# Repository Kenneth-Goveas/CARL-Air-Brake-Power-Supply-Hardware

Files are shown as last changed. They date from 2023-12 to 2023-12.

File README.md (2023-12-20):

# CARL Air Brake Power Supply Hardware

This repository contains the electronic hardware design for the power supply
module of the [CARL Air Brake][cab-repo] computer. The CARL Air Brake computer
automatically controls a rocket air brake in flight, so that the vehicle attains
an apogee at the desired altitude. The power supply module distributes
electrical power to all systems in the computer.

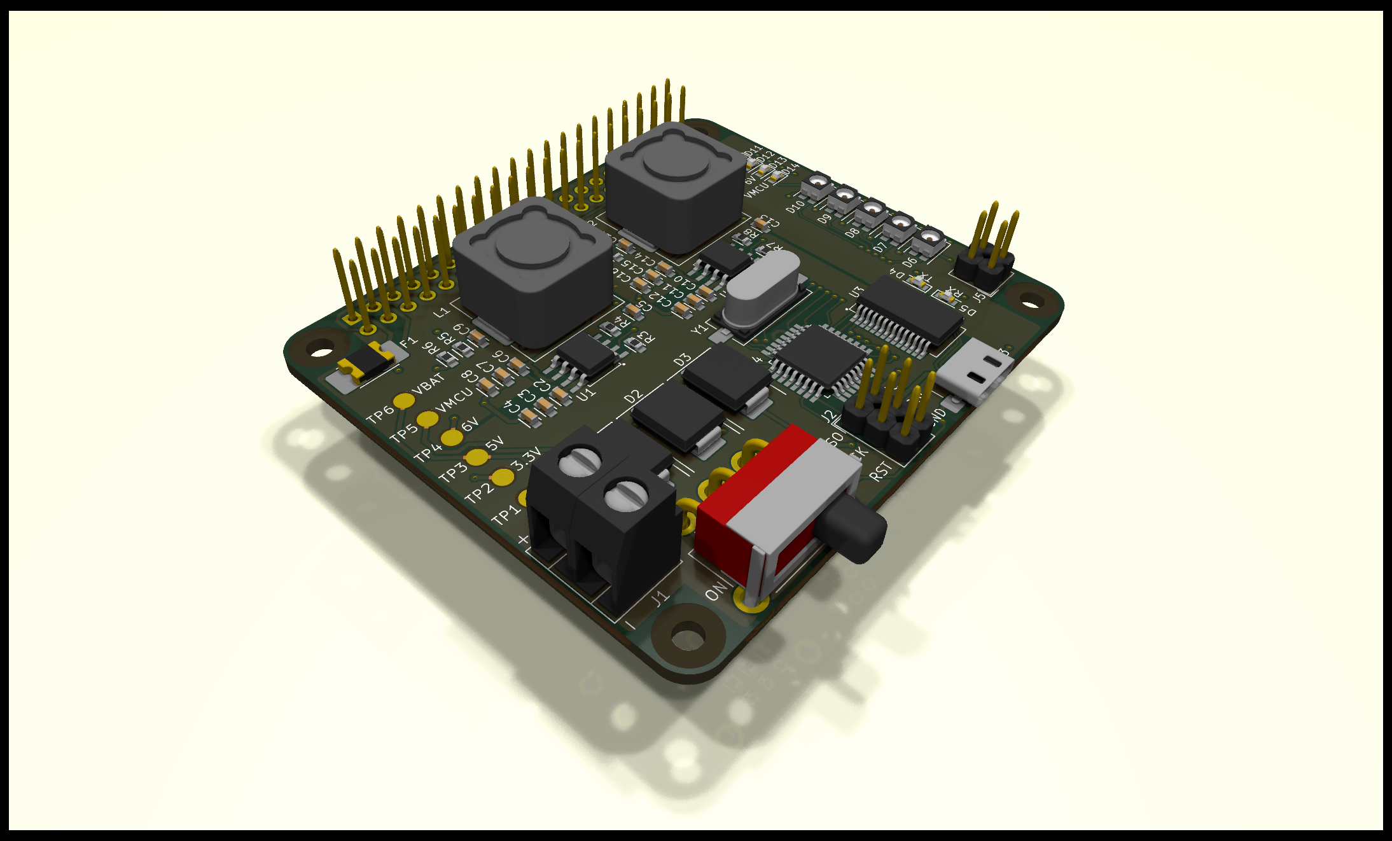
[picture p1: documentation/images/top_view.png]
Top view of the power supply module


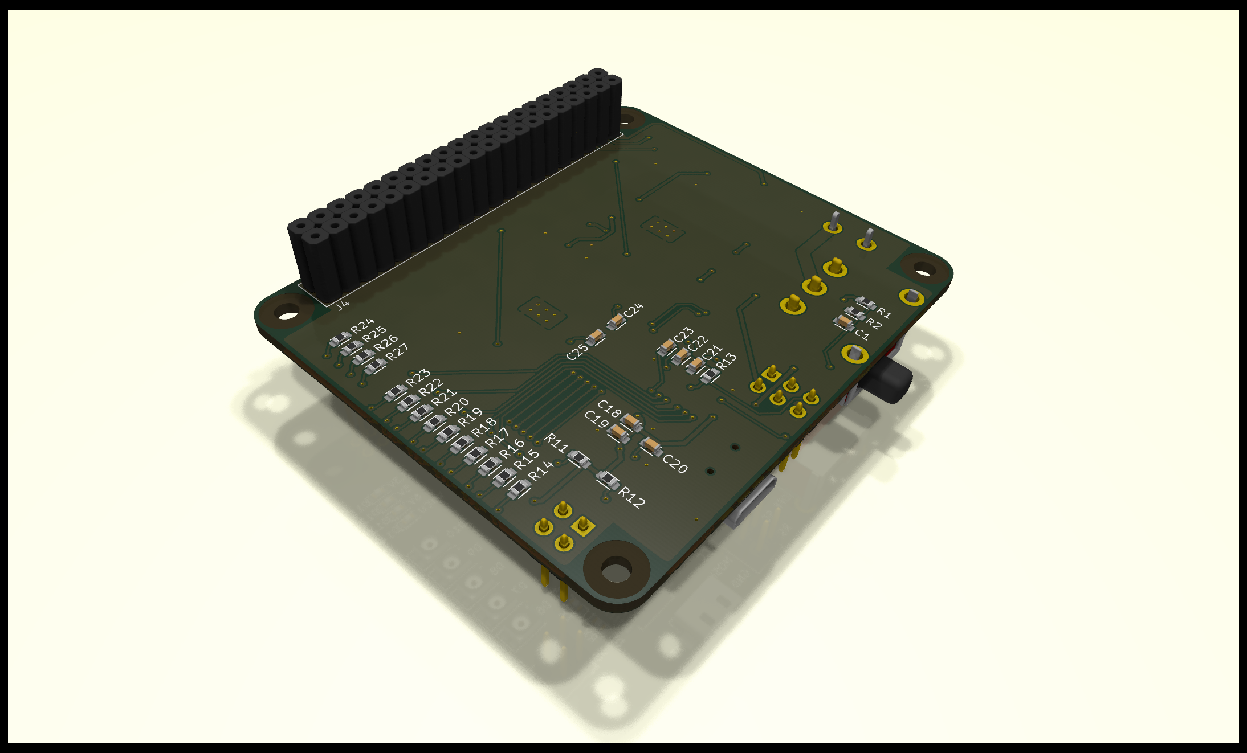
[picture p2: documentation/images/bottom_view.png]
Bottom view of the power supply module


Detailed documentation for this repository can be found in the following files.

- [description.md][des]:
  Detailed description of the power supply module.
- [cloning.md][cln]:
  Properly cloning this repository along with all its submodules.
- [prerequisites.md][req]:
  Necessary software for viewing and editing the electronic design.
- [organization.md][org]:
  Directory structure and organization of files in this repository.
- [flashing.md][fsh]:
  Flashing software onto the power supply module.

[des]:      ./documentation/description.md
[cln]:      ./documentation/cloning.md
[req]:      ./documentation/prerequisites.md
[org]:      ./documentation/organization.md
[fsh]:      ./documentation/flashing.md

[cab-repo]: https://github.com/Kenneth-Goveas/CARL-Air-Brake

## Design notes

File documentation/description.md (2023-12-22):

# Description

The CARL Air Brake computer is comprised of the following three circuit boards.
These boards are loaded with their respective software and connected by stacking
on top of each other, to make up the computer.

- Peripheral devices module.
- Power supply module.
- Raspberry Pi 3 model A+.

This repository contains the electronic design for the second of the above three
boards. Other electronic designs and software are contained in different
repositories (for more details, see [CARL Air Brake][cab-repo]).

## Overview

The power supply module supplies regulated power to all systems in the CARL Air
Brake computer. It also has status LEDs to indicate which of the onboard power
lines are live. After being flashed with its associated software, it also
monitors the battery voltage and indicates the same on another LED array. When
the battery is fully charged, all these LEDs light up in green. As the voltage
drops, they turn red one by one. When all these LEDs turn red, they also start
flashing to indicate to the user that the battery needs charging.

## Battery

The power supply module is intended for use with a lithium polymer battery with
the following specifications.

| **Specification** | **Value** |
| --- | --- |
| Cells in series | 3 |
| Nominal voltage | 11.1V |
| Fully charged voltage | 12.6V |
| Continuous discharge current  | >1.5A |

## Components

The relevant circuit components on the board are marked on the following diagram
and described below.

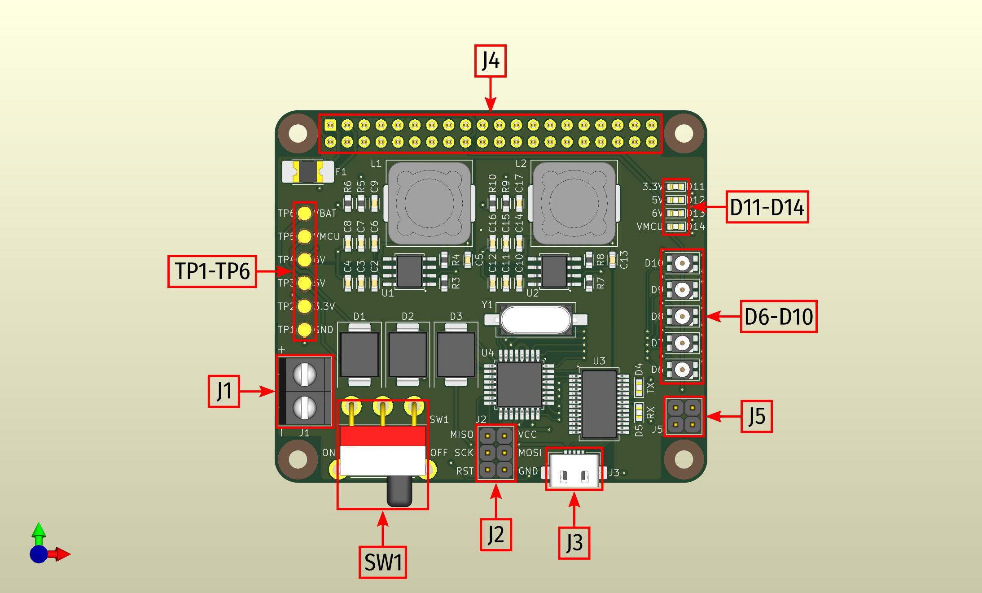
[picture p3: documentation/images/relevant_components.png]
Relevant components of the power supply module


| **Designation** | **Description** |
| --- | --- |
| J1 | Screw terminal for battery connection. |
| J2 | Port for ICSP cable for programming. |
| J3 | Port for USB cable for programming. |
| J4 | Stacking header for connecting other boards. |
| J5 | Header for supplying 6V to peripheral devices module. |
| SW1 | Switch for making/breaking battery connection. |
| D6-D10 | Battery voltage indication LEDs. |
| D11-D14 | Power line status LEDs. |
| TP1-TP6 | Test points for measuring power line voltages. |

## Working

The following is a simple block diagram of the power supply module.

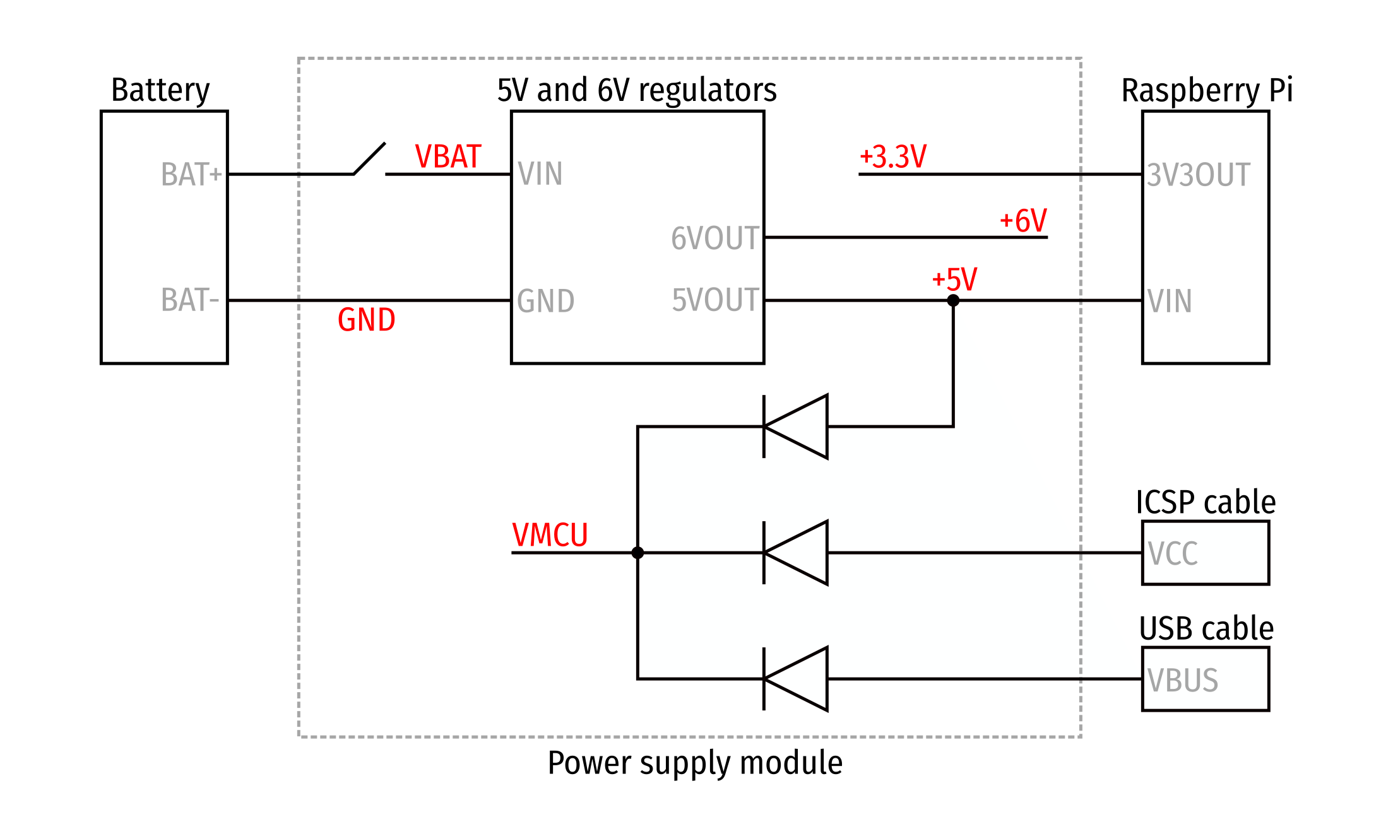
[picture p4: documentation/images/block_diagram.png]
Block diagram of the power supply module


As seen in the above diagram, the board contains the following five power lines.
Note that the line voltages listed below are nominal values. It is normal for
the actual voltages to deviate slightly.

| **Name**  | **Description** | **Voltage** |
| --- | --- | --- |
| VBAT | Positive terminal of battery. | Battery voltage |
| +3.3V | Output of 3.3V regulator on Raspberry Pi. | 3.3V |
| +5V | Output of onboard 5V regulator. | 5V |
| +6V | Output of onboard 6V regulator. | 6V |
| VMCU | Power line for onboard microcontroller. | 5V |

When the battery is connected and the switch turned on, the VBAT, VMCU, +5V, and
+6V lines become live. If, in addition to the battery, the Raspberry Pi is also
connected, then the +3.3V line also becomes live. If any or both of the two
programming cables are connected, the VMCU line becomes live regardless of
whether or not the battery is connected. Thus, the VMCU line has three power
sources - the battery, and two programming cables. It is safe to simultaneously
connect more than one of these power sources as the board has protection diodes
that will prevent any short circuit.

The Raspberry Pi draws power from the +5V line. The Raspberry Pi has an onboard
3.3V regulator which supplies power to the +3.3V line. The peripheral devices
module draws power from the +3.3V, +5V, and +6V lines. The VMCU line supplies
power to the onboard microcontroller of the power supply module, and its
associated circuitry. Each regulated power line is also connected to a separate
status LED (D11-D14) to visually indicate which lines are live. Additionally,
all power and GND lines are connected to separate test points (TP1-TP6) for
measuring their voltages with a multimeter.

The onboard microcontroller is programmable from the two ports J2 and J3. When
flashed with the appropriate software (see [flashing.md][fsh]), it measures the
battery voltage and accordingly drives the indication LEDs (D6-D10), resulting
in the behavior described in [Overview](#overview).

[fsh]:      ./flashing.md

[cab-repo]: https://github.com/Kenneth-Goveas/CARL-Air-Brake

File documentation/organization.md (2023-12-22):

# Organization

Upon properly cloning this repository according to the instructions in
[cloning.md][cln], you should end up with the following directory structure.

```
CARL-Air-Brake-Power-Supply-Hardware/
|__ CARL-Air-Brake-Power-Supply-Hardware.kicad_pro
|__ CARL-Air-Brake-Power-Supply-Hardware.kicad_sch
|__ CARL-Air-Brake-Power-Supply-Hardware.kicad_pcb
|__ production/
|   |__ CARL-Air-Brake-Power-Supply-Hardware.bom.csv
|   |__ CARL-Air-Brake-Power-Supply-Hardware.boardoutline.ger
|   |__ CARL-Air-Brake-Power-Supply-Hardware.toplayer.ger
|   |__ CARL-Air-Brake-Power-Supply-Hardware.bottomlayer.ger
|   |__ CARL-Air-Brake-Power-Supply-Hardware.topsoldermask.ger
|   |__ CARL-Air-Brake-Power-Supply-Hardware.bottomsoldermask.ger
|   |__ CARL-Air-Brake-Power-Supply-Hardware.toppaste.ger
|   |__ CARL-Air-Brake-Power-Supply-Hardware.bottompaste.ger
|   |__ CARL-Air-Brake-Power-Supply-Hardware.topsilkscreen.ger
|   |__ CARL-Air-Brake-Power-Supply-Hardware.bottomsilkscreen.ger
|   |__ CARL-Air-Brake-Power-Supply-Hardware.drills_pth.xln
|   |__ CARL-Air-Brake-Power-Supply-Hardware.holes_npth.xln
|__ fp-lib-table -> ./library/fp-lib-table
|__ sym-lib-table -> ./library/sym-lib-table
|__ library/
|   |__ symbols/
|   |__ footprints/
|   |__ models/
|   |__ fp-lib-table
|   |__ sym-lib-table
|   |__ README.md
|__ README.md
|__ documentation/
    |__ images/
    |__ description.md
    |__ cloning.md
    |__ prerequisites.md
    |__ organization.md
    |__ flashing.md
```

The KiCad project, schematic, and board files are located in the root directory.
The bill of materials file, and the gerber and drill files for production are
located in the [production][prod-dir] directory. The KiCad component library
[KiCad Libraries][lib-repo] is contained as a submodule in the
[library][lib-dir] directory. Symbolic links [fp-lib-table][fp-lnk] and
[sym-lib-table][sym-lnk] in the root directory point to the library table files
[fp-lib-table][fp-file] and [sym-lib-table][sym-file] in the [library][lib-dir]
directory. These symbolic links are required for KiCad to be able to locate the
component library.

[cln]:      ./cloning.md

[prod-dir]: ../production

[fp-lnk]:   ../fp-lib-table
[sym-lnk]:  ../sym-lib-table
[fp-file]:  ../library/fp-lib-table
[sym-file]: ../library/sym-lib-table

[lib-dir]:  ../library
[lib-repo]: https://github.com/Kenneth-Goveas/KiCad-Libraries

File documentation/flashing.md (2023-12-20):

# Flashing

The software for the power supply module can be found in the
[CARL Air Brake Power Supply Software][cab-psup-sw-repo] repository. This
repository contains two programs - a tuning program, and a main program - that
can be flashed onto the board. The tuning program is used to calibrate the
voltage thresholds at which the indication LEDs should turn red. The main
program is used to monitor the battery voltage and drive the LEDs as described
in [description.md][des]. For detailed instructions for flashing the software,
see [CARL Air Brake Power Supply Software][cab-psup-sw-repo].

[des]:              ./description.md

[cab-psup-sw-repo]: https://github.com/Kenneth-Goveas/CARL-Air-Brake-Power-Supply-Software

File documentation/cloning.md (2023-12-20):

# Cloning

This repository contains symbolic links, and also includes other repositories as
submodules. Therefore, special care needs to be taken to properly clone this
repository onto a local system. In particular, Git must be configured to
preserve symbolic links, and submodules must be cloned recursively.

## Configuring Git

The following command configures Git to preserve symbolic links. On Windows, it
may also be necessary to enable [Developer mode][win-dev-mode] to allow the
creation of symbolic links.

```
git config --global core.symlinks true
```

## Cloning recursively

Once Git is configured as above, the following command properly clones this
repository along with all its submodules. Note that the `--recurse-submodules`
option is passed to clone submodules recursively.

```
git clone --recurse-submodules \
  https://github.com/Kenneth-Goveas/CARL-Air-Brake-Power-Supply-Hardware.git
```

[win-dev-mode]: https://learn.microsoft.com/en-us/windows/apps/get-started/enable-your-device-for-development

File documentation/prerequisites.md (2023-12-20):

# Prerequisites

The electronic design in this repository was created with [KiCad 7.0][kicad],
which must be installed on your system in order to view and edit the design.
Installation instructions can be found on the [Download][kicad-dl] page.

Additionally, the [Fira Sans Condensed][fira] font was used in the KiCad
schematic and symbol editors instead of the default font. This is because the
default font occupies more space, making it difficult to fit the schematic on
the page. Once installed, this font can be selected in KiCad by clicking on
*Preferences > Preferences > Schematic Editor > Display Options* and choosing
from the *Default font* drop down menu.

[kicad]:    https://www.kicad.org
[kicad-dl]: https://www.kicad.org/download

[fira]:     https://fonts.google.com/specimen/Fira+Sans+Condensed

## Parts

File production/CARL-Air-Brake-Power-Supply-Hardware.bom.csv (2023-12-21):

Serial | Reference | Manufacturer | Part | Description | Quantity
1 | R24 | Yageo | AC0603FR-0768RL | Resistor 68Ohm 100mW 1% 0603 | 1
2 | R14 R15 R16 R17 R18 R19 R20 R21 R22 R23 R25 R27 | Yageo | RC0603FR-10150RL | Resistor 150Ohm 100mW 1% 0603 | 12
3 | R26 | Yageo | RC0603FR-07200RL | Resistor 200Ohm 100mW 1% 0603 | 1
4 | R11 R12 | Yageo | RT0603DRE07430RL | Resistor 430Ohm 100mW 0.5% 0603 | 2
5 | R2 R3 R7 R13 | Yageo | RT0603FRE1310KL | Resistor 10kOhm 100mW 1% 0603 | 4
6 | R1 | Yageo | RC0603FR-1320KL | Resistor 20kOhm 100mW 1% 0603 | 1
7 | R6 R10 | Yageo | RT0603BRD0750KL | Resistor 50kOhm 100mW 0.1% 0603 | 2
8 | R4 R8 | Yageo | RC0603FR-07100KL | Resistor 100kOhm 100mW 1% 0603 | 2
9 | R5 | Yageo | AC0603FR-07365KL | Resistor 365kOhm 100mW 1% 0603 | 1
10 | R9 | Yageo | RC0603FR-07453KL | Resistor 453kOhm 100mW 1% 0603 | 1
11 | C9 C17 | Murata | GRM1885C1H5R0WA01D | Capacitor 5pF 50V 1% 0603 | 2
12 | C24 C25 | Murata | GRM1885C1H300GA01D | Capacitor 30pF 50V 2% 0603 | 2
13 | C4 C6 C12 C14 C19 C20 C23 | Murata | GCM188R71C104JA37D | Capacitor 0.1uF 16V 5% 0603 | 7
14 | C5 C13 | Murata | GRM188R61A474JA61D | Capacitor 0.47uF 10V 5% 0603 | 2
15 | C1 C2 C3 C10 C11 C18 C21 C22 | Murata | GRT188R61C106KE13J | Capacitor 10uF 16V 10% 0603 | 8
16 | C7 C8 C15 C16 | Murata | GRM188R61A226ME15D | Capacitor 22uF 10V 20% 0603 | 4
17 | L1 L2 | Eaton | DR127-3R3-R | Inductor 3.3uH 10.5A (rms) 21.5A (sat) 20% | 2
18 | F1 | Bourns | MF-MSMF260-2 | Fuse PTC 2.6A (hold) 5.2A (trip) 6V 1812 | 1
19 | D1 D2 D3 | Diotec | SK84-AQ | Diode Schottky 0.55V @ 8A DO-214AB/SMC | 3
20 | D4 D5 | Ams Osram | LW Q38G-Q1OO-3K6L-1 | LED White 2.85V @ 5mA 0603 | 2
21 | D11 D12 D13 D14 | Wuerth | 150060AS75000 | LED Amber 2V @ 20mA 0603 | 4
22 | D6 D7 D8 D9 D10 | Wuerth | 150141RV73100 | LED Red Green 2V @ 20mA | 5
23 | Y1 | ECS | ECS-160-20-5PX-TR | Crystal 16Mhz 20pF HC49-US | 1
24 | J2 | Adam Tech | PH2-06-UA | Pin Header 2x3 | 1
25 | J1 | CUI | TB003-500-P02BE | Screw Terminal 2-Pin | 1
26 | J3 | Wuerth | 629105136821 | Micro USB Receptacle | 1
27 | J4 | Adafruit | 2223 | Stacking Header 2x20 | 1
28 | J5 | Wuerth | 61300421121 | Pin Header 2x2 | 1
29 | SW1 | Salecom | T80-S-TS-13P-A1-2-R-E-H | Switch SPDT | 1
30 | U1 U2 | TI | TPS56528DDAR | Buck converter | 2
31 | U3 | FTDI | FT232RNL-REEL | USB-UART Bridge | 1
32 | U4 | Microchip | ATmega328P-AU | 8-Bit AVR Microcontroller | 1

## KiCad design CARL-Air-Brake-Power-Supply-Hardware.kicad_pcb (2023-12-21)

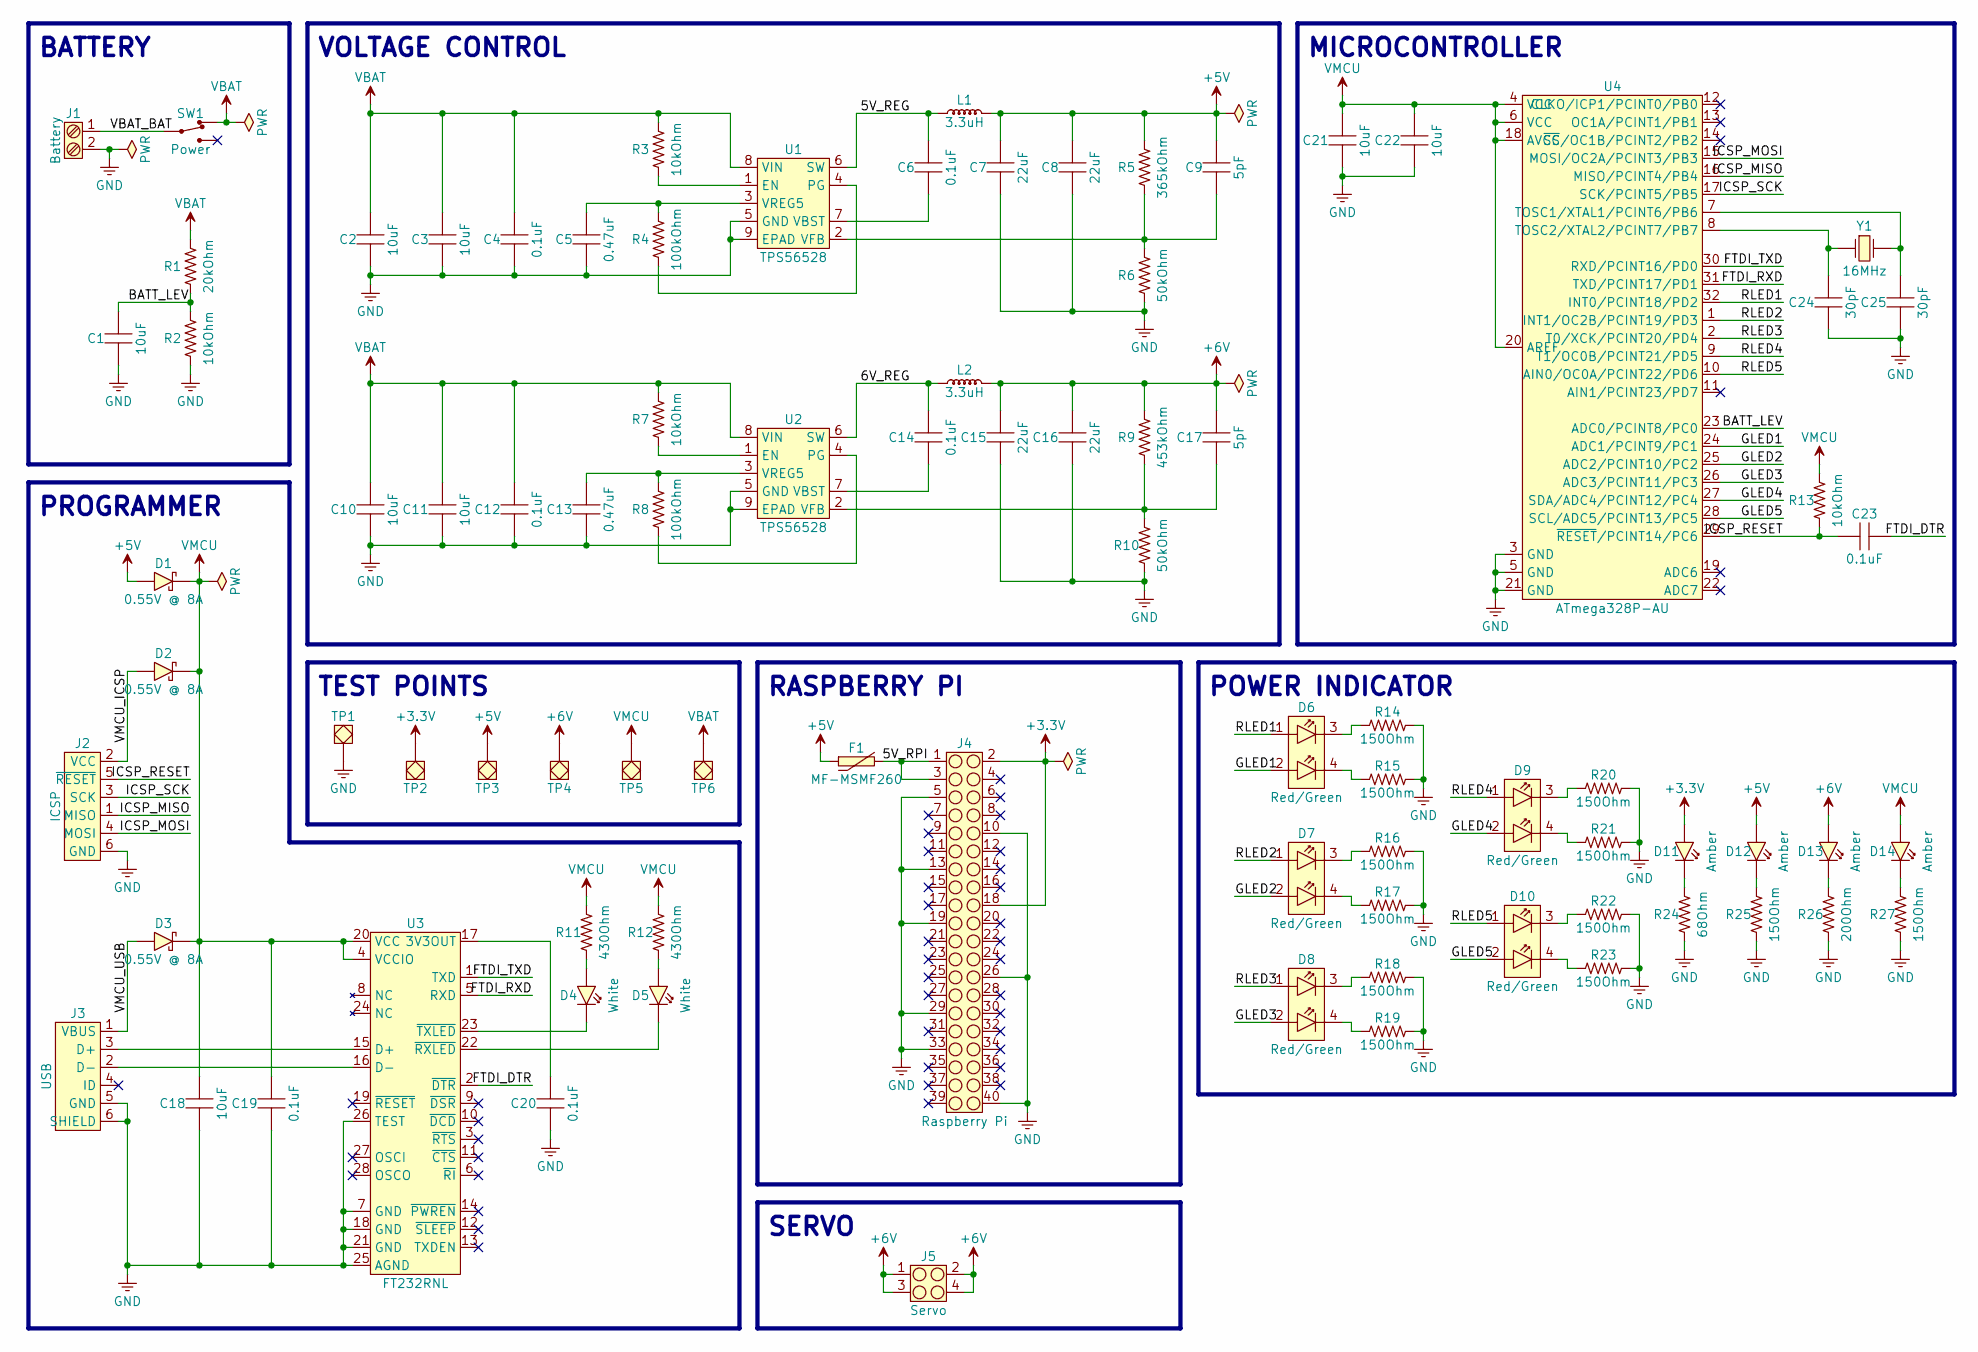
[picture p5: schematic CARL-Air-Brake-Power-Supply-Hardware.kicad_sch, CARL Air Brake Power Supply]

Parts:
C1, C2, C3, C10, C11, C18, C21, C22: 10uF; Cap_Ceramic_0603
C4, C6, C12, C14, C19, C20, C23: 0.1uF; Cap_Ceramic_0603
C5, C13: 0.47uF; Cap_Ceramic_0603
C7, C8, C15, C16: 22uF; Cap_Ceramic_0603
C9, C17: 5pF; Cap_Ceramic_0603
C24, C25: 30pF; Cap_Ceramic_0603
D1, D2, D3: 0.55V @ 8A; Diode_DO-214AB_SMC
D4, D5: White; LED_0603
D6, D7, D8, D9, D10: Red/Green; LED_Dual_Wuerth_WL-SBTW
D11, D12, D13, D14: Amber; LED_0603
F1: MF-MSMF260; Fuse_PTC_1812
J1: Battery; ScrewTerm_02_CUI_TB003-500-02BK
J2: ICSP; PinHead_02x03_Pitch2.54mm_Bot3.00mm_Top6.00mm_Shroud2.50mm
J3: USB; USB_Micro_B_Recp_Wuerth_629105136821
J4: Raspberry Pi; StackHead_02x20_Pitch2.54mm_Bot10.50mm_Top8.50mm
J5: Servo; PinHead_02x02_Pitch2.54mm_Bot3.00mm_Top6.00mm_Shroud2.50mm
L1, L2: 3.3uH; Ind_Eaton_DR127
R1: 20kOhm; Res_Film_0603
R2, R3, R7, R13: 10kOhm; Res_Film_0603
R4, R8: 100kOhm; Res_Film_0603
R5: 365kOhm; Res_Film_0603
R6, R10: 50kOhm; Res_Film_0603
R9: 453kOhm; Res_Film_0603
R11, R12: 430Ohm; Res_Film_0603
R14, R15, R16, R17, R18, R19, R20, R21, R22, R23, R25, R27: 150Ohm; Res_Film_0603
R24: 68Ohm; Res_Film_0603
R26: 200Ohm; Res_Film_0603
SW1: Power; Switch_SPDT_Salecom_T80-S-TS-13P-A1-2-R
TP1, TP2, TP3, TP4, TP5, TP6: TestPoint_CircPad2.00mm_CircMsk2.50mm
U1, U2: TPS56528; SOIC_08_Dim4.00x5.00x1.70mm_Pitch1.27mm_RectThPad2.95x4.90m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
U3: FT232RNL; SOIC_28_Dim5.50x10.50x2.00mm_Pitch0.65mm
U4: ATmega328P-AU; TQFP_08x08_Dim7.00x7.00x1.20mm_Pitch0.80mm
Y1: 16MHz; Crystal_HC49-US

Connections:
/5V_REG: C6.2, L1.1, U1.6 (SW)
/5V_RPI: F1.2, J4.1, J4.3
/6V_REG: C14.2, L2.1, U2.6 (SW)
/BATT_LEV: C1.2, R1.1, R2.2, U4.23 (ADC0/PCINT8/PC0)
/FTDI_DTR: C23.2, U3.2 (~DTR)
/FTDI_RXD: U3.5 (RXD), U4.31 (TXD/PCINT17/PD1)
/FTDI_TXD: U3.1 (TXD), U4.30 (RXD/PCINT16/PD0)
/GLED1: D6.2 (A), U4.24 (ADC1/PCINT9/PC1)
/GLED2: D7.2 (A), U4.25 (ADC2/PCINT10/PC2)
/GLED3: D8.2 (A), U4.26 (ADC3/PCINT11/PC3)
/GLED4: D9.2 (A), U4.27 (SDA/ADC4/PCINT12/PC4)
/GLED5: D10.2 (A), U4.28 (SCL/ADC5/PCINT13/PC5)
/ICSP_MISO: J2.1 (MISO), U4.16 (MISO/PCINT4/PB4)
/ICSP_MOSI: J2.4 (MOSI), U4.15 (MOSI/OC2A/PCINT3/PB3)
/ICSP_RESET: C23.1, J2.5 (~RESET), R13.1, U4.29 (~RESET/PCINT14/PC6)
/ICSP_SCK: J2.3 (SCK), U4.17 (SCK/PCINT5/PB5)
/RLED1: D6.1 (A), U4.32 (INT0/PCINT18/PD2)
/RLED2: D7.1 (A), U4.1 (INT1/OC2B/PCINT19/PD3)
/RLED3: D8.1 (A), U4.2 (T0/XCK/PCINT20/PD4)
/RLED4: D9.1 (A), U4.9 (T1/OC0B/PCINT21/PD5)
/RLED5: D10.1 (A), U4.10 (AIN0/OC0A/PCINT22/PD6)
/VBAT_BAT: J1.1, SW1.2
/VMCU_ICSP: D2.1 (A), J2.2 (VCC)
/VMCU_USB: D3.1 (A), J3.1 (VBUS)
unnamed: D4.1 (A), R11.1
unnamed: D4.2 (K), U3.23 (~TXLED)
unnamed: D5.1 (A), R12.1
unnamed: D5.2 (K), U3.22 (~RXLED)
unnamed: D6.3 (K), R14.1
unnamed: D6.4 (K), R15.1
unnamed: D7.3 (K), R16.1
unnamed: D7.4 (K), R17.1
unnamed: D8.3 (K), R18.1
unnamed: D8.4 (K), R19.1
unnamed: D9.3 (K), R20.1
unnamed: D9.4 (K), R21.1
unnamed: D10.3 (K), R22.1
unnamed: D10.4 (K), R23.1
unnamed: D11.2 (K), R24.2
unnamed: D12.2 (K), R25.2
unnamed: D13.2 (K), R26.2
unnamed: D14.2 (K), R27.2
unnamed: J3.3 (D+), U3.15 (D+)
unnamed: J3.2 (D-), U3.16 (D-)
unnamed: R3.1, U1.1 (EN)
unnamed: R4.1, U1.4 (PG)
unnamed: C6.1, U1.7 (VBST)
unnamed: C9.1, R5.1, R6.2, U1.2 (VFB)
unnamed: C5.2, R4.2, U1.3 (VREG5)
unnamed: R7.1, U2.1 (EN)
unnamed: R8.1, U2.4 (PG)
unnamed: C14.1, U2.7 (VBST)
unnamed: C17.1, R9.1, R10.2, U2.2 (VFB)
unnamed: C13.2, R8.2, U2.3 (VREG5)
unnamed: C20.2, U3.17 (3V3OUT)
unnamed: C25.2, U4.7 (TOSC1/XTAL1/PCINT6/PB6), Y1.2
unnamed: C24.2, U4.8 (TOSC2/XTAL2/PCINT7/PB7), Y1.1

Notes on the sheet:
BATTERY
MICROCONTROLLER
TEST POINTS
RASPBERRY PI
PROGRAMMER
POWER INDICATOR
SERVO
VOLTAGE CONTROL

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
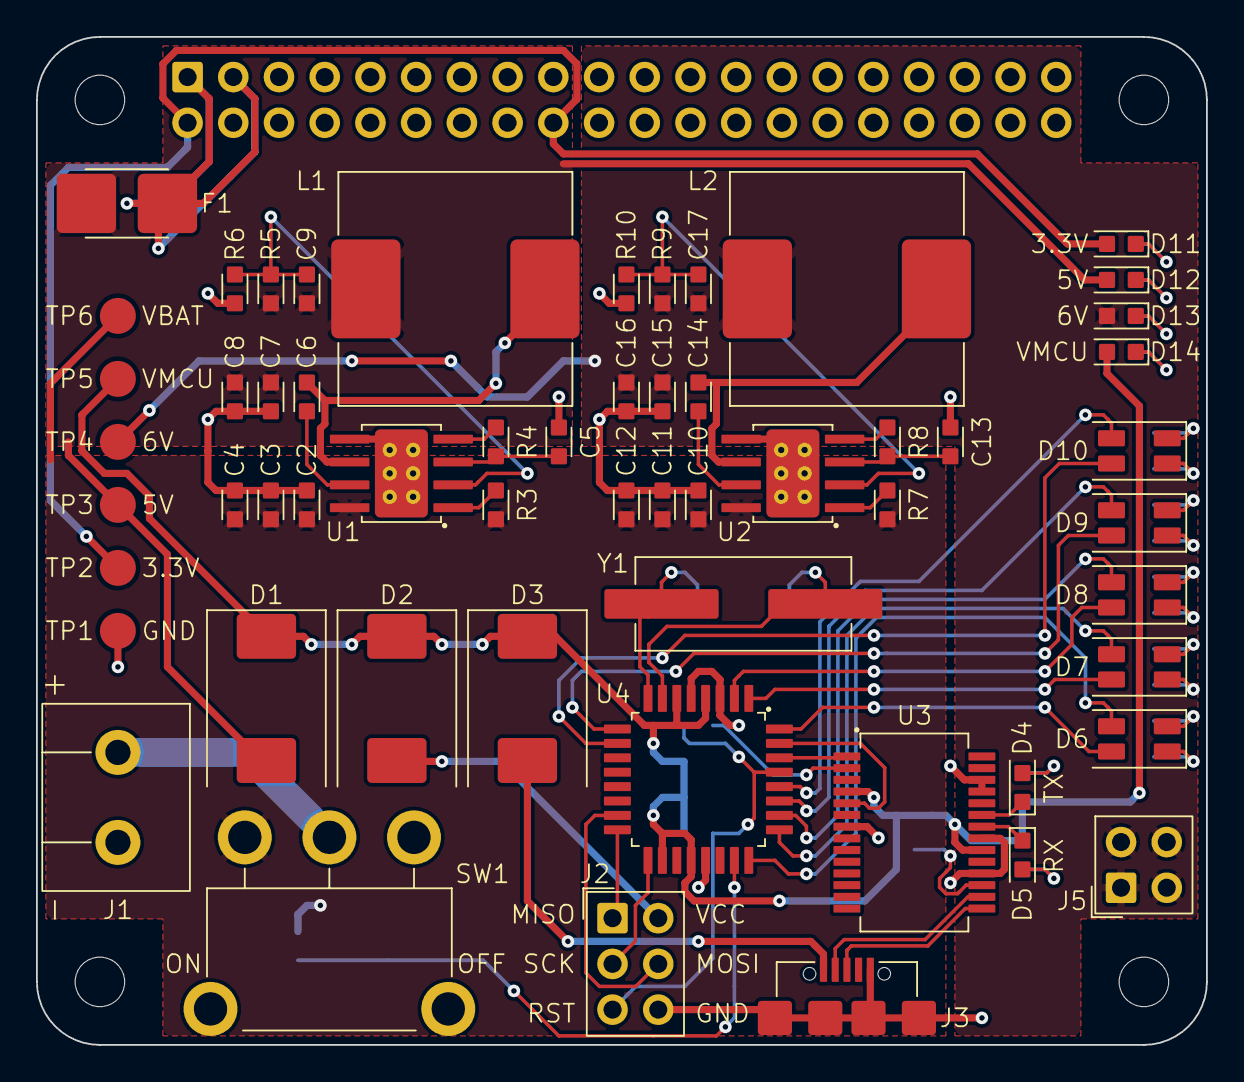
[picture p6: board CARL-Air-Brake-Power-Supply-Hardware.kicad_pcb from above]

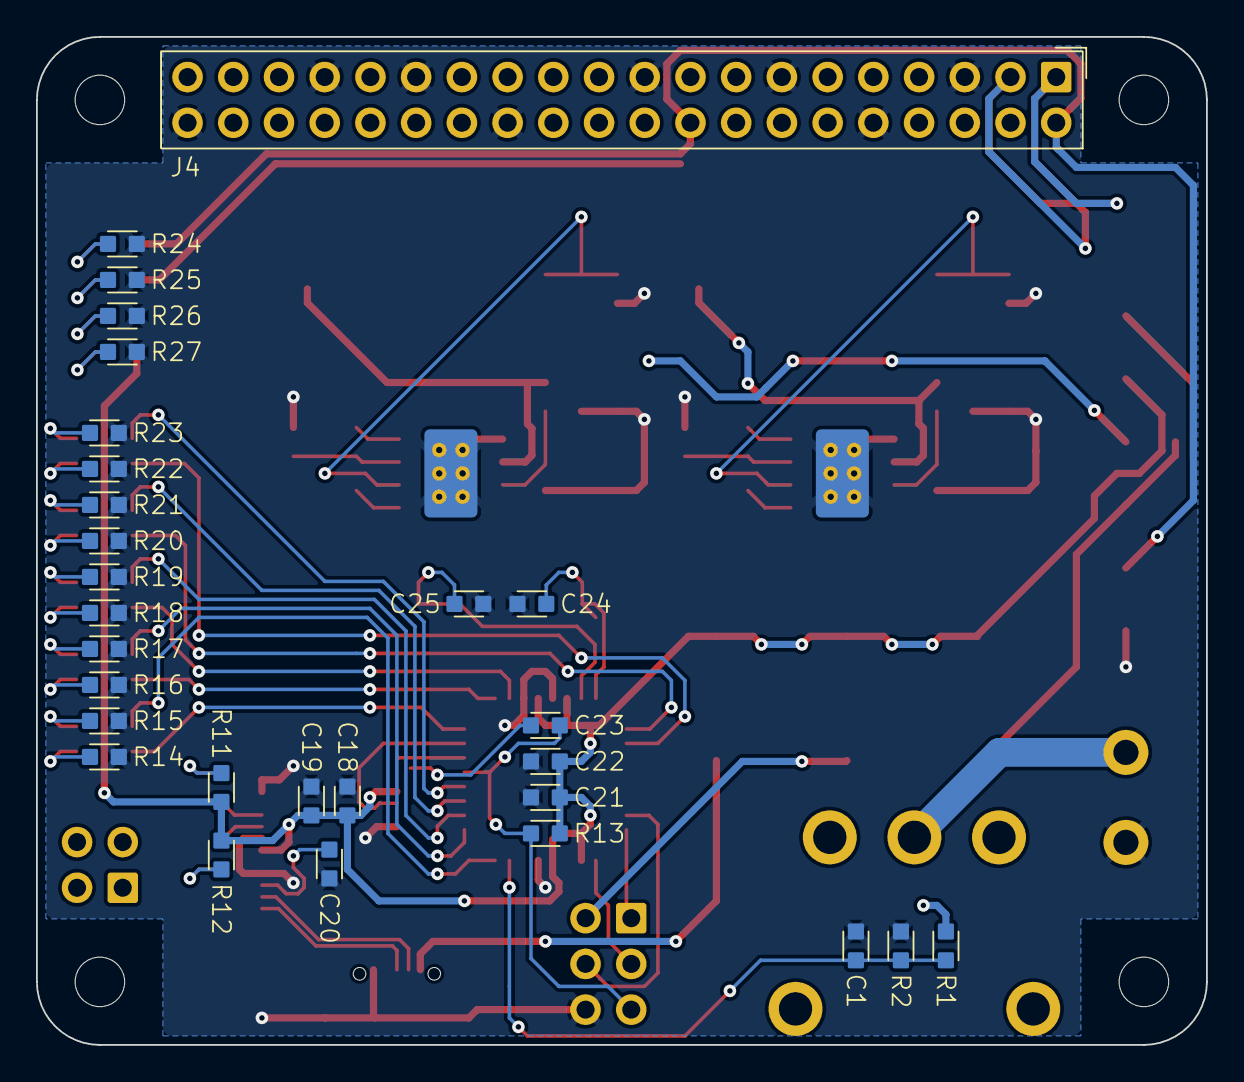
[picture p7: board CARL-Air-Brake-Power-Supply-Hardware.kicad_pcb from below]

Board: 2 copper layers, 65.0 x 56.0 mm, 86 parts (29 on the bottom side), 63 nets.

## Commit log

2023-12-07 Added KiCad library
    Cloned KiCad component library as submodule.
2023-12-07 Initialized KiCad project
    Created KiCad project files without any circuit design.
    [CARL-Air-Brake-Power-Supply-Hardware.kicad_pcb, CARL-Air-Brake-Power-Supply-Hardware.kicad_sch]
2023-12-08 Added schematic
    Completed circuit schematic and performed ERC.
    [CARL-Air-Brake-Power-Supply-Hardware.kicad_sch]
2023-12-08 Assigned footprints
    Assigned footprints to all symbols in circuit schematic.
    [CARL-Air-Brake-Power-Supply-Hardware.kicad_sch]
2023-12-10 Arranged components
    Created board layout and placed components at suitable locations.
    [CARL-Air-Brake-Power-Supply-Hardware.kicad_pcb]
2023-12-11 Added test point for VBAT
    Added test point for VBAT line and updated PCB accordingly.
    [CARL-Air-Brake-Power-Supply-Hardware.kicad_pcb, CARL-Air-Brake-Power-Supply-Hardware.kicad_sch]
2023-12-11 Added filled zones
    Added filled copper zones for high current power supply lines.
    [CARL-Air-Brake-Power-Supply-Hardware.kicad_pcb]
2023-12-13 Routed circuit board
    Completed circuit design by routing all connections, and performed DRC.
    [CARL-Air-Brake-Power-Supply-Hardware.kicad_pcb]
2023-12-20 Added local settings file to gitignore
    Removed local settings file *.kicad_prl and added it to gitignore.
2023-12-20 Changed VBUS to VMCU
    Changed name of VBUS net to VMCU in schematic and board files.
    [CARL-Air-Brake-Power-Supply-Hardware.kicad_pcb, CARL-Air-Brake-Power-Supply-Hardware.kicad_sch]
2023-12-20 Corrected component values
    Corrected resistance values of resistors R6 and R10.
    [CARL-Air-Brake-Power-Supply-Hardware.kicad_pcb, CARL-Air-Brake-Power-Supply-Hardware.kicad_sch]
2023-12-21 Added bill of materials
    Created production directory and added bill of materials.
    [bill-of-materials.csv]
2023-12-21 Added DRC rule to flag drills inside courtyards
    Modified DRC rules to flag the presence of PTH or NPTH drills inside
    footprint courtyards as errors instead of ignoring them. Performed DRC
    after making this update.
2023-12-21 Plotted gerber and drill files
    Configured settings for gerber and drill file generation and plotted
    gerber and drill files.
    [CARL-Air-Brake-Power-Supply-Hardware.kicad_pcb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]
2023-12-21 Renamed BOM file
    Renamed bill of materials file to match naming convention used in other
    production-related files.
    [CARL-Air-Brake-Power-Supply-Hardware.bom.csv]
2023-12-22 Added temporary files to gitignore
    Added entries in gitignore for lock files generated by KiCad and swap
    files generated by Vim.
